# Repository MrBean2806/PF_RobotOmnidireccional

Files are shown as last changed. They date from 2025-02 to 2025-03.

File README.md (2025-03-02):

# PF_RobotOmnidireccional
## Proyecto Final de Grado - Ingeniería Electrónica
## _"Sistema de Control de Tracción de Bajo Nivel para un Robot Móvil"_

<div style="text-align: center;">
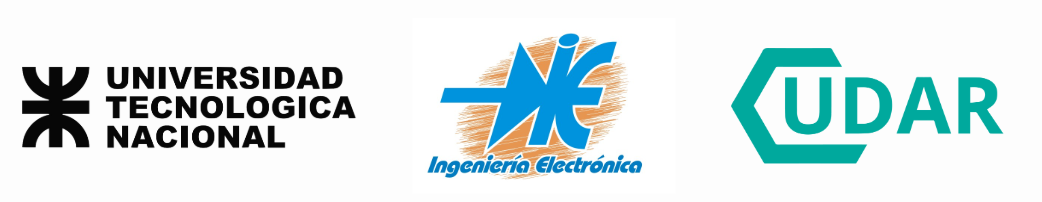
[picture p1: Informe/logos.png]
  
</div>

### Introducción
El proyecto se centra en el desarrollo de un sistema de control de tracción de bajo nivel para un robot móvil. Su principal objetivo es transformar los comandos de velocidad provenientes de la Computadora de Navegación en velocidades individuales para cada motor. Además, el sistema ejecuta un lazo de control de
velocidad en cada rueda, midiendo y ajustando la tensión media aplicada a cada motor. Finalmente, el sistema envía datos de velocidad estimada y aceleración a
la Computadora de Navegación. 

Este proyecto forma parte de una iniciativa más amplia del Centro Universitario
de Automatización y Robótica (CUDAR) de la UTN FRC, que abarca el diseño, desarrollo y construcción de un sistema de odometría multi-cámara montado en
un robot móvil, destinado a encontrar trayectorias eficientes en ambientes desconocidos y dinámicos.

### Contexto
A continuación se presenta el diagrama de contexto del sistema, que muestra
las entidades externas con las que éste interactúa y la naturaleza de dichas interacciones.

<div style="text-align: center;">
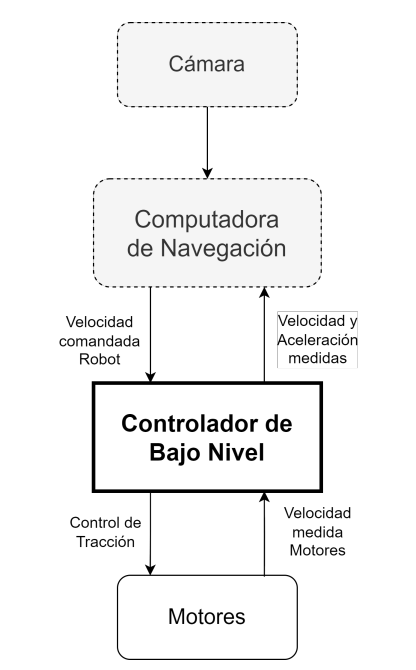
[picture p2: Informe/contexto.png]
  
</div>

Puede observarse que el sistema interactúa directamente con las siguientes entidades externas:
La Computadora de navegación (CDN), que provee la velocidad comandada y recibe la velocidad estimada y la aceleración medida por el Controlador de Bajo Nivel (CBN).
La gravedad y la aceleración, que son medidas para el uso de la Computadora de Navegación.
Los Motores del robot móvil, cuya velocidad es seteada y medida por el sistema.

### Arquitectura de Software

En la siguiente figura se muestra el diagrama conceptual de este proyecto, en el cual se pueden apreciar dos caminos principales.

<div style="text-align: center;">
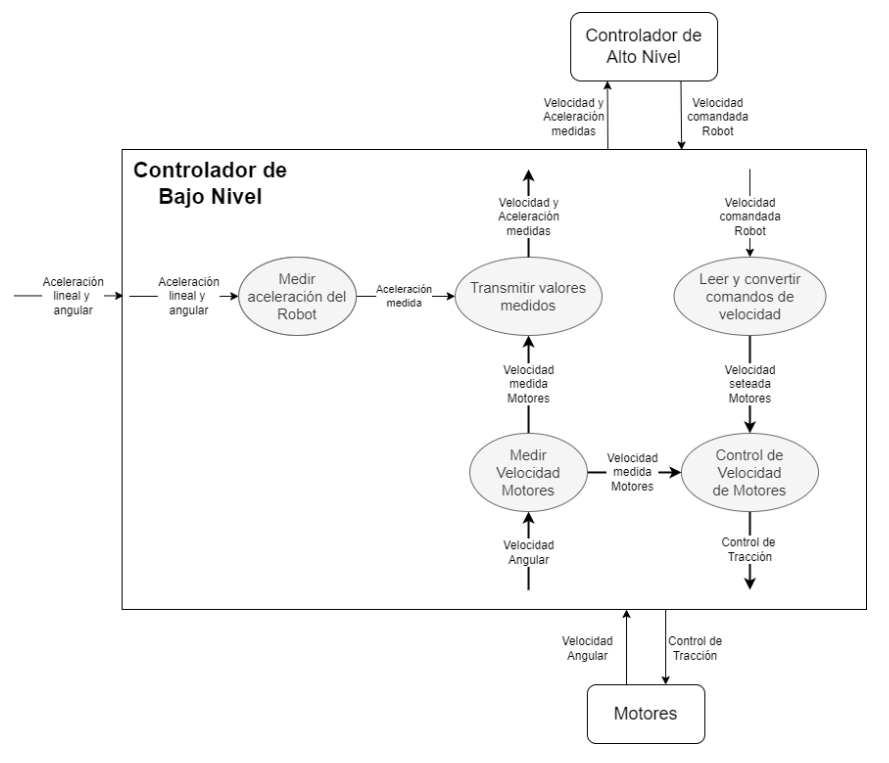
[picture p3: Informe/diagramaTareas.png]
  
</div>

En primer lugar, la velocidad comandada es enviada por la CDN y recibida por el CBN, la cual es convertida en comandos de velocidad para cada motor y finalmente se envía una señal para controlar los motores, teniendo en cuenta el valor de la velocidad medida de estos últimos. 

En segunda instancia, se miden tanto los valores de velocidad de cada motor, como los valores de aceleraciones del robot, los cuales son enviados finalmente al CDN.

_Para una explicación más detallada referirse al informe completo en la carpeta "Informe"_

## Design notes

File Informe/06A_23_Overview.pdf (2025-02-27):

### Universidad Tecnologica

´

### Nacional

### Facultad Regional Cordoba

´

# Proyecto Final

# Sistema de Control de Tracción de Bajo Nivel para un Robot Móvil

# Overview

### Profesores: Ing. Encina, Lucas Esteban Ing. Galleguillo, Juan Cayetano del Corazón Dr. Gaydou, David Alejandro

### Director de proyecto: Ing. Gutierrez, Guillermo

### Alumnos: Arias, Manuel Exequiel - 85187 Bean, Agustín - 78806

### 4 de julio de 2023

Proyecto Final | Overview

2

Proyecto Final | Overview

## 1. Overview

El proyecto descripto se basa en un sistema de control de tracción de bajo nivel para un robot móvil.
El propósito del mismo es convertir los comandos de velocidad enviados por un Controlador de Alto Nivel en velocidades individuales para cada motor. A su vez, se encarga de ejecutar un lazo de control de velocidad en cada rueda midiendo ésta y variando la tensión media aplicada a cada motor. Por último, envía datos recolectados de velocidad estimada y aceleración al Controlador de Alto Nivel.

El proyecto presentado está enmarcado dentro de uno más amplio, perteneciente al Centro Universitario de Automatización y Robótica (CUDAR) de la UTN FRC. El proyecto completo consiste en el diseño, desarrollo y construcción de un sistema de odometría multi-cámara, montado en un robot móvil, para encontrar trayectorias eficientes en ambientes desconocidos y dinámicos.

### 1.1. Contexto

A continuación se presenta el diagrama de contexto del sistema, que muestra las entidades externas con las que éste interactúa y la naturaleza de dichas interacciones.

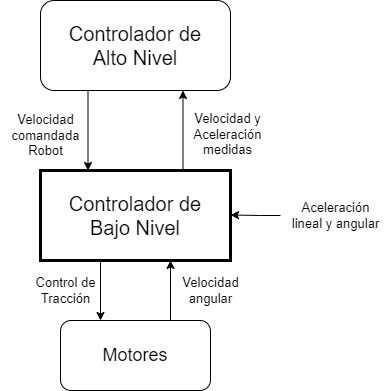
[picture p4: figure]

Figura 1: Diagrama de contexto

Puede observarse que el sistema interactúa directamente con las siguientes entidades externas:

El Controlador de Alto Nivel (CAN), que provee la velocidad comandada y recibe la velocidad estimada y la aceleración medida por el Controlador de Bajo Nivel (CBN).

3

Proyecto Final | Overview

La gravedad y la aceleración, que son medidas para el uso del Controlador de Alto Nivel.

Los Motores del robot móvil, cuya velocidad es seteada y medida por el sistema.

### Variables monitoreadas y controladas

Nombre | Tipo | Representación Física
Velocidad comandada Robot | Monitoreada Velocidad global deseada
| | recibida desde el CAN
Aceleración/Gravedad | Monitoreada Aceleración lineal y angular del
| | robot
Velocidad Angular Motores | Monitoreada Velocidad angular de cada
| | Motor
Velocidad y aceleración medidas Controlada | Velocidad y aceleración medidas
| | por el CBN que son enviadas al CAN
Tracción Motores | Controlada | Excitación aplicada a cada Motor

Cuadro 1: Variables monitoreadas y controladas preliminares

### 1.2. Metas

Las metas de alto nivel del sistema son:

G1 - Medir la velocidad y aceleración del robot y transmitir estos datos al Controlador de Alto Nivel.

G2 - Controlar la velocidad individual de los motores de forma que la velocidad global cumpla con la comandada por el Controlador de Alto Nivel.

## 2. Conceptos Operacionales

Caso de Uso 1: Inicialización de los Controladores
Este caso de uso describe cómo se configura el robot para que esté preparado para su operación normal.

Actor primario: Operario.

Precondición:
El robot está desenergizado.

4

Proyecto Final | Overview

Poscondición:
El robot está energizado.
Los controladores de alto y bajo nivel están inicializados y comunicados entre sí. El robot no se encuentra en movimiento.
El controlador de bajo nivel está desactivado.

Principal escenario exitoso:

1. El operador enciende el robot.
2. Ambos controladores se inicializan y activan sus módulos de comunicación.
3. El CBN inicializa sus módulos y periféricos.
4. Los controladores establecen una comunicación bidireccional entre sí.

Caso de Uso 2: Operación Normal del Controlador
Este caso de uso describe la operación normal del controlador de bajo nivel.

Actor primario: Controlador de Alto Nivel.

Precondición:
El robot está energizado.
El robot no se encuentra en movimiento
Los controladores de alto y bajo nivel están inicializados y comunicados entre sí El controlador de bajo nivel está desactivado

Poscondición: El robot no se encuentra en movimiento
El controlador de bajo nivel está desactivado

Principal escenario exitoso:

1. El CAN envía la señal de activación al de bajo nivel.
2. El CBN ingresa en su modo normal de operación.
3. El CBN recibe comandos de velocidad global y ajusta la velocidad de los Motores para cumplir con ella.
4. El CBN realiza mediciones de aceleración y velocidad y las transmite al CAN.
5. El CAN finaliza su operación y desactiva el CBN.

Caso de Uso 3: Mantener la velocidad seteada por el CAN
Este caso de uso describe cómo los comandos de velocidad global enviados por el

5

Proyecto Final | Overview

CAN son convertidos a señales de control adecuadas para los motores.

Actor primario: Controlador de Bajo Nivel.

Precondición:
Los controladores de alto y bajo nivel están inicializados y comunicados entre sí.

Poscondición:
Los controladores de alto y bajo nivel están inicializados y comunicados entre sí. La velocidad global del robot se condice con la comandada por el CAN.

Principal escenario exitoso:

1. El CBN recibe el comando de velocidad del CAN.
2. El CBN calcula las señales de control necesarias para cada Motor individual.
3. El CBN ejecuta un lazo de control comparando la señal calculada con la velocidad medida de cada Motor.
4. El CBN aplica la excitación correspondiente a cada Motor.
5. Se repiten los pasos del 1 al 4.

Caso de Uso 4: Realizar mediciones y enviarlas al CAN
Este caso de uso describe cómo el CBN realiza mediciones de velocidad de los Motores y de aceleración del robot y las envía al CAN.

Actor primario: Controlador de Bajo Nivel.

Precondición:
Los controladores de alto y bajo nivel están inicializados y comunicados entre sí.

Poscondición:
Los controladores de alto y bajo nivel están inicializados y comunicados entre sí. La velocidad global del robot se condice con la comandada por el CAN.

Principal escenario exitoso:

1. El CBN realiza la medición de aceleración angular y lineal.
2. El CBN realiza la medición de velocidad angular de cada motor.
3. El CBN envía los datos recolectados en los apartados anteriores al CAN.
4. Se repiten los pasos del 1 al 3.

6

Proyecto Final | | | | Overview

## 3. Entidades Externas

### Controlador de Alto Nivel

El Controlador de Alto Nivel envía comandos de velocidad al Controlador de Bajo Nivel, y recibe los datos de velocidad y aceleración transmitidos por éste.

Nombre | Tipo | Rango | Unidad | Interpretación Física
Velocidad comandada Robot | | | | Comando de Velocidad para el robot
Velocidad lineal (módulo) | Real [0...2.0] | m/s
Velocidad lineal (ángulo) | Real | [0...2π] | rad

Velocidad angular
(módulo) | Real [0...5.0] | rad/s

Cuadro 2: Variables Monitoreadas del Controlador de Bajo Nivel para el Controlador de Alto Nivel

Nombre | Tipo | Rango | Unidad | Interpretación Física
Velocidad Global estimada | | | | Velocidad calculada del robot con las mediciones efectuadas
Velocidad lineal (módulo) | Real [0...2.0] | m/s
Velocidad lineal (ángulo) | Real | [0...2π] | rad

Velocidad angular
(módulo) | Real [0...5.0] | rad/s

Cuadro 3: Variables Controladas del Controlador de Bajo Nivel para el Controlador de Alto Nivel

### Motores

Los motores de corriente continua son controlados por el CBN, y son los encargados de que el robot se desplace a la velocidad seteada por el CAN.

Nombre | Tipo | Rango | Unidad | Interpretación Física
Velocidad angular Real [-5.0...5.0] | rad/s | Velocidad angular del eje de cada Motor

Cuadro 5: Variables monitoreadas del Controlador de Bajo Nivel para los Motores

7

Proyecto Final | Overview
Nombre | Tipo | Rango | Unidad | Interpretación Física
Control de Tracción Real [0...1.00] | - | Ciclo de trabajo de la señal
| | | | PWM aplicada a cada motor

Cuadro 4: Variables controladas del Controlador de Bajo Nivel para los Motores

## 4. Requisitos Funcionales del Sistema

El Controlador de Bajo Nivel realiza 5 funciones de sistema: medir la aceleración del robot, medir la velocidad de los Motores, transmitir los valores medidos, leer y convertir comandos de velocidad, y el control de velocidad de los Motores.

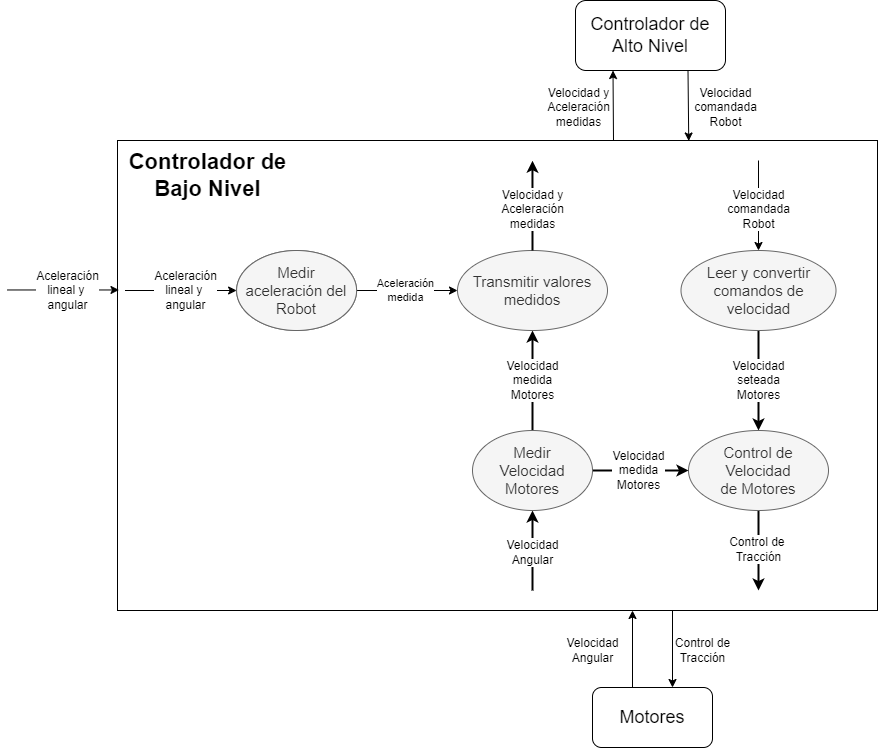
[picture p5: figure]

Figura 2: Funciones del sistema

Este sistema mide la aceleración del robot y la velocidad de cada Motor, para luego transmitirlas al Controlador de Alto Nivel. Este a su vez envía comandos ´

8

Proyecto Final | Overview

de velocidad, que son comparados con la velocidad medida de cada Motor para ajustar la tracción de los mismos de forma acorde.
Los requisitos de alto nivel para la función del Controlador de Bajo Nivel son:

REQ-CBN-1: El Controlador de Bajo Nivel deberá proveer el valor de la velocidad y la aceleración medida.
Motivo: Los valores de velocidad y aceleración del robot son críticos para que el Controlador de Alto Nivel pueda operar correctamente.

REQ-CBN-2: El Controlador de Bajo Nivel deberá setear el Control de Tracción.
Motivo: Para cumplir con la velocidad comandada por el Controlador de Alto Nivel es necesario ajustar la tracción de los Motores de forma acorde.
Nombre | Tipo Rango | Unidad Interpretación Física

Aceleración
medida | Real | [-10.0...10.0] m/s² | Aceleración medida del robot

Velocidad medida
Motores | Real | [-5.0...5.0] | rad/s | Velocidad angular medida en cada Motor

Velocidad seteada
Motores | Real | [-5.0...5.0] | rad/s | Velocidad angular seteada para cada Motor

Cuadro 6: Variables internas de la función del CBN

9

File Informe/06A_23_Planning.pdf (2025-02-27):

Id | Nombre de tarea | Duración | Comienzo | Fin
1 | Definición de requerimientos | 36 días | vie 12/5/23 | vie 30/6/23
2 | Diseño Conceptual | 26 días | vie 26/5/23 | vie 30/6/23
3 | Diseño de Arquitectura de Hardware | 10 días | lun 3/7/23 | vie 14/7/23
4 | Desarrollo de Hardware21 días | lun 17/7/23 | lun 14/8/23
5 | Diseño de Arquitectura de Software | 10 días | lun 17/7/23 | vie 28/7/23
6 | Desarrollo de Software | 21 días | lun 31/7/23 | lun 28/8/23
7 | Integración y puesta en marcha | 7 días | mar 29/8/23 | mié 6/9/23
8 | Validación y Ensayo | 2 días | jue 7/9/23 | vie 8/9/23
30 | 7 | 14 | 21 | 28 | 4 | 11 | 18 | 25 | 2 | 9 | 16 | 23 | 30 | 6 | 13 | 20 | 27 | 3 | 10
may '23 | jun '23 | jul '23 | ago '23 | sep '23

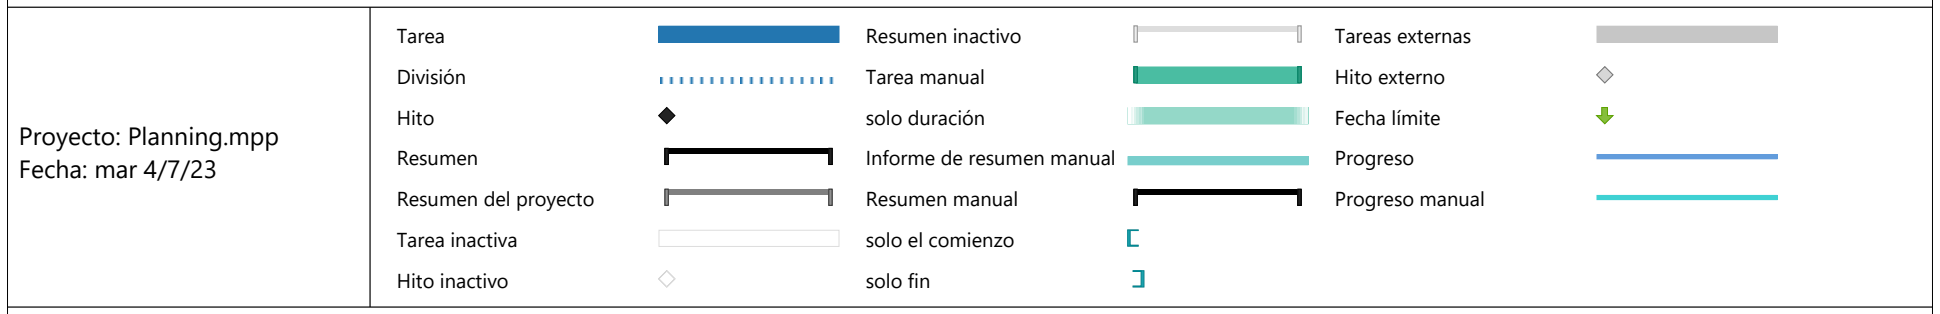
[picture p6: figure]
Tarea; División; Hito; Resumen; Resumen del proyecto; Tarea inactiva; Hito inactivo; Resumen inactivo; Tarea manual; solo duración; Informe de resumen manual; Resumen manual; solo el comienzo; solo fin; Tareas externas; Hito externo; Fecha límite; Progreso; Progreso manual; Proyecto: Planning.mpp Fecha: mar 4/7/23

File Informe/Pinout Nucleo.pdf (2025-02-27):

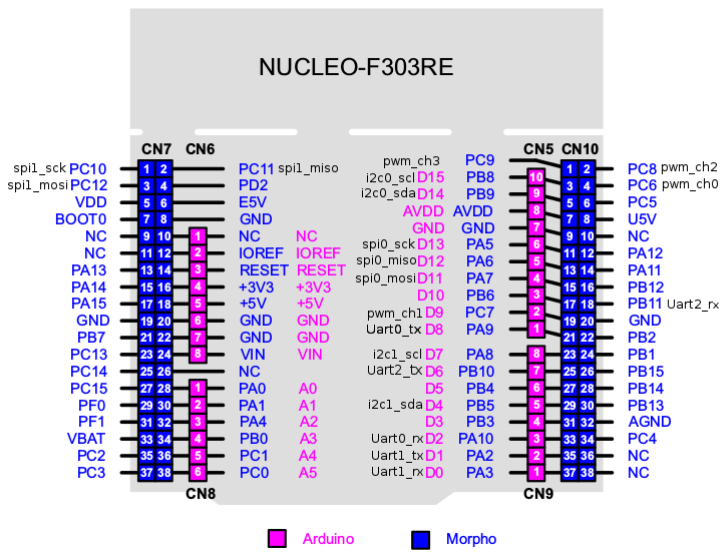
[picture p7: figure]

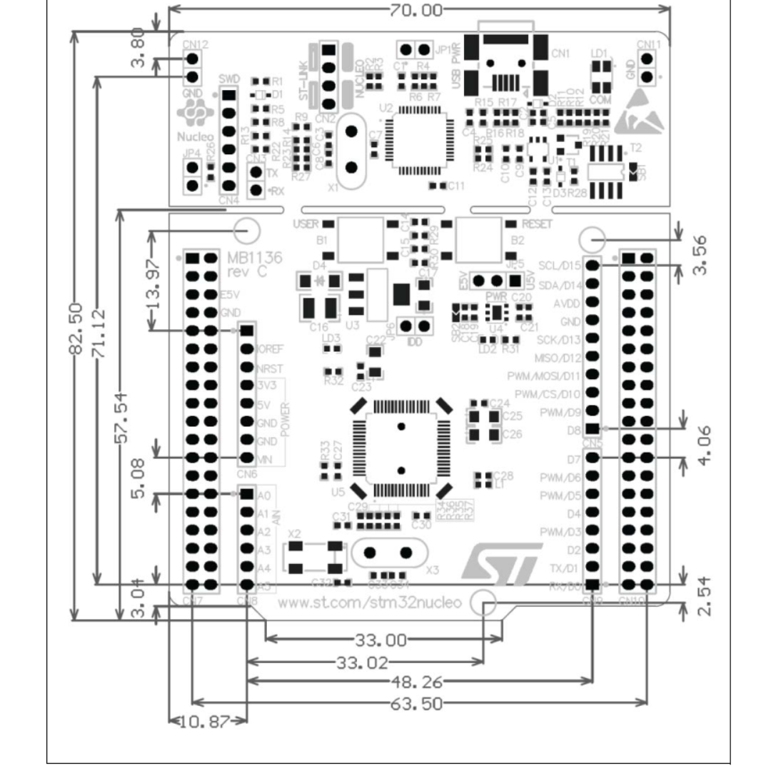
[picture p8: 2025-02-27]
Informe/Dimensiones Nucleo.png

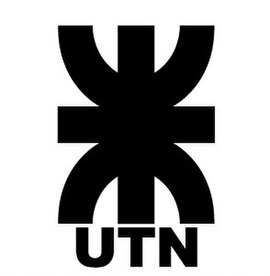
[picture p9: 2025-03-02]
Informe/utn.png

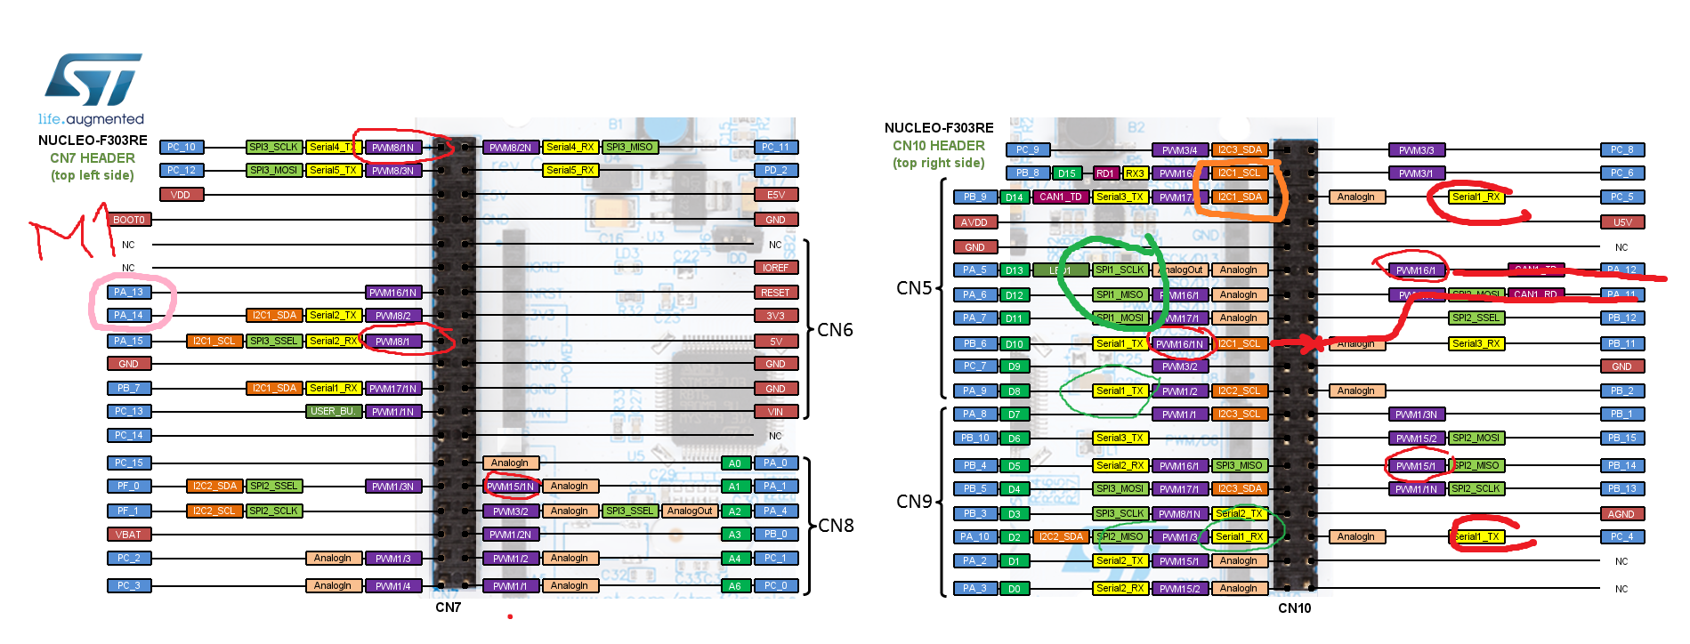
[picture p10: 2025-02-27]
Informe/Pinout Nucleo Completo.png

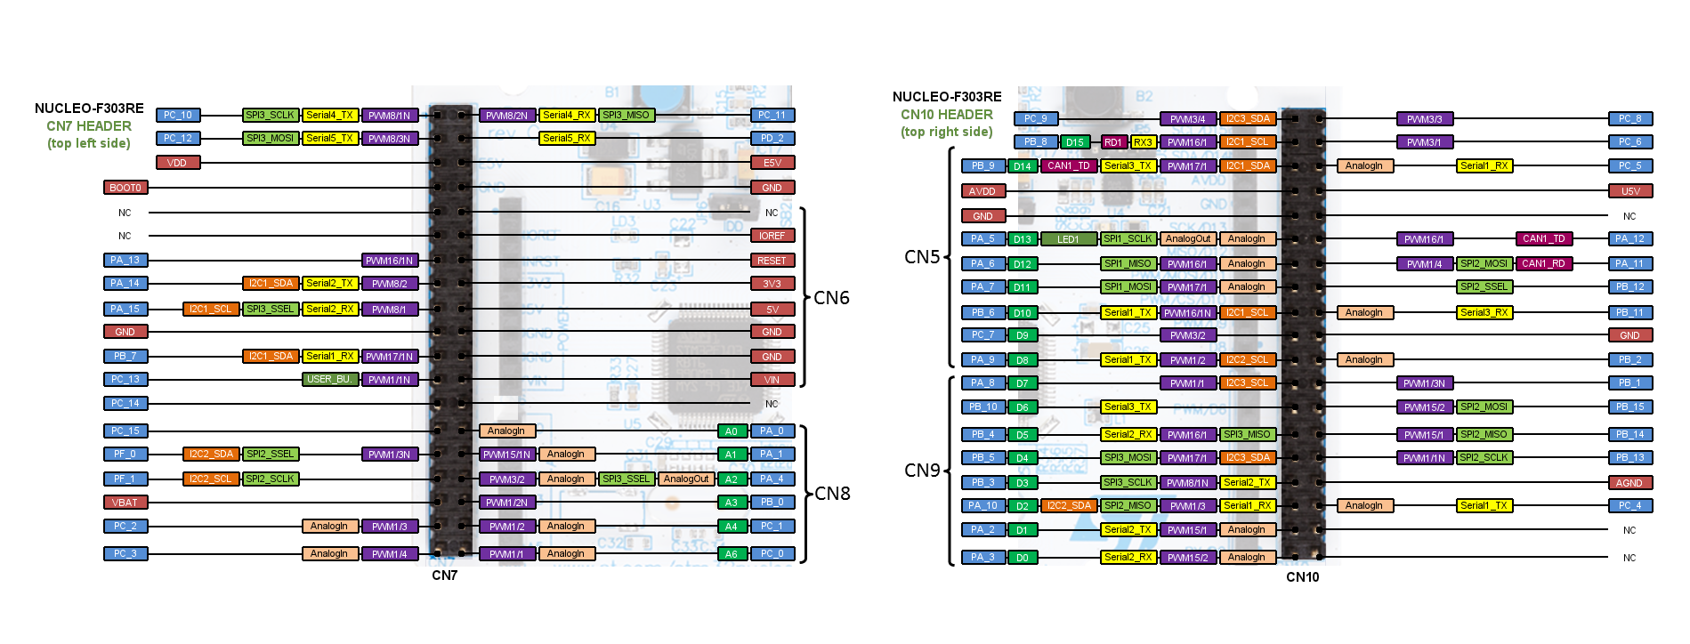
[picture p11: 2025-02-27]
Informe/Pinout Nucleo Completo v1.png

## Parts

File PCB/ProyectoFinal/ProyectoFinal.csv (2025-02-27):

Source: | C:\Users\agusb\OneDrive\Escritorio\Proyecto Final\PCB\ProyectoFinal\ProyectoFinal.kicad_sch
Date: | 26/11/2023 19:50:53
Tool: | Eeschema (6.0.10)
Generator: | C:\Program Files\KiCad\6.0\bin\scripting\plugins/bom_csv_grouped_by_value.py
Component Count: | 33
Individual Components:
Item | Qty | Reference(s) | Value | LibPart | Footprint | Datasheet
 |  | C1 | 100n | Device:C | Capacitor_THT:C_Disc_D4.3mm_W1.9mm_P5.00mm | ~
 |  | D1 | LED | Device:LED | LED_THT:LED_D5.0mm | ~
 |  | J1 | Conector_Alim_PuenteH1 | Connector:Conn_01x02_Female | Connector_JST:JST_EH_B2B-EH-A_1x02_P2.50mm_Vertical | ~
 |  | J2 | Conector_Encoder1 | Connector:Conn_01x04_Male | Connector_JST:JST_EH_B4B-EH-A_1x04_P2.50mm_Vertical | ~
 |  | J3 | Conector_Encoder3 | Connector:Conn_01x04_Male | Connector_JST:JST_EH_B4B-EH-A_1x04_P2.50mm_Vertical | ~
 |  | J4 | Conector_Alim_PuenteH2 | Connector:Conn_01x02_Female | Connector_JST:JST_EH_B2B-EH-A_1x02_P2.50mm_Vertical | ~
 |  | J5 | Conector_Encoder2 | Connector:Conn_01x04_Male | Connector_JST:JST_EH_B4B-EH-A_1x04_P2.50mm_Vertical | ~
 |  | J6 | Conector_Encoder4 | Connector:Conn_01x04_Male | Connector_JST:JST_EH_B4B-EH-A_1x04_P2.50mm_Vertical | ~
 |  | J7 | Conector_Motor1 | Connector:Conn_01x02_Female | Connector_PinHeader_2.54mm:PinHeader_1x02_P2.54mm_Vertical | ~
 |  | J8 | Conector_Motor2 | Connector:Conn_01x02_Female | Connector_PinHeader_2.54mm:PinHeader_1x02_P2.54mm_Vertical | ~
 |  | J9 | Conector_Motor3 | Connector:Conn_01x02_Female | Connector_PinHeader_2.54mm:PinHeader_1x02_P2.54mm_Vertical | ~
 |  | J10 | Conector_Motor4 | Connector:Conn_01x02_Female | Connector_PinHeader_2.54mm:PinHeader_1x02_P2.54mm_Vertical | ~
 |  | J12 | Conector_Baterias | Connector:Conn_01x02_Male | Connector_JST:JST_EH_B2B-EH-A_1x02_P2.50mm_Vertical | ~
 |  | J14 | Conector_IMU | Connector_Generic:Conn_02x08_Odd_Even | CustomLib:Conector_IMU | ~
 |  | J15 | Conector_ConversorUSB | Connector:Conn_01x06_Female | Connector_PinSocket_2.54mm:PinSocket_1x06_P2.54mm_Horizontal | ~
 |  | J16 | Conector_Programador | Connector:Conn_01x04_Male | Connector_PinSocket_2.54mm:PinSocket_1x04_P2.54mm_Vertical | ~
 |  | R1 | 10k | Device:R | Resistor_THT:R_Axial_DIN0207_L6.3mm_D2.5mm_P10.16mm_Horizontal | ~
 |  | R2 | 10k | Device:R | Resistor_THT:R_Axial_DIN0207_L6.3mm_D2.5mm_P10.16mm_Horizontal | ~
 |  | R3 | 220 | Device:R | Resistor_THT:R_Axial_DIN0207_L6.3mm_D2.5mm_P10.16mm_Horizontal | ~
 |  | R4 | 220 | Device:R | Resistor_THT:R_Axial_DIN0207_L6.3mm_D2.5mm_P10.16mm_Horizontal | ~
 |  | R5 | 10k | Device:R | Resistor_THT:R_Axial_DIN0207_L6.3mm_D2.5mm_P10.16mm_Horizontal | ~
 |  | R6 | 10k | Device:R | Resistor_THT:R_Axial_DIN0207_L6.3mm_D2.5mm_P10.16mm_Horizontal | ~
 |  | R7 | 220 | Device:R | Resistor_THT:R_Axial_DIN0207_L6.3mm_D2.5mm_P10.16mm_Horizontal | ~
 |  | R8 | 220 | Device:R | Resistor_THT:R_Axial_DIN0207_L6.3mm_D2.5mm_P10.16mm_Horizontal | ~
 |  | R9 | R | Device:R | Resistor_THT:R_Axial_DIN0207_L6.3mm_D2.5mm_P10.16mm_Horizontal | ~
 |  | R10 | R | Device:R | Resistor_THT:R_Axial_DIN0207_L6.3mm_D2.5mm_P10.16mm_Horizontal | ~
 |  | R11 | R | Device:R | Resistor_THT:R_Axial_DIN0207_L6.3mm_D2.5mm_P10.16mm_Horizontal | ~
 |  | R12 | 4K7 | Device:R | Resistor_THT:R_Axial_DIN0207_L6.3mm_D2.5mm_P10.16mm_Horizontal | ~
 |  | R13 | 4K7 | Device:R | Resistor_THT:R_Axial_DIN0207_L6.3mm_D2.5mm_P10.16mm_Horizontal | ~
 |  | SW1 | SW_SPST | Switch:SW_SPST | CustomLib:SW_SPST | ~
 |  | U1 | INA219_Module | CustomLib:INA219_Module | CustomLib:INA219_Module
 |  | U2 | LM2596_Module | CustomLib:LM2596_Module | CustomLib:DCDC_StepDown_LM2596
 |  | U3 | Nucleo_F303RE | CustomLib:Nucleo_F303RE | CustomLib:Nucleo_F303RE
Collated Components:
Item | Qty | Reference(s) | Value | LibPart | Footprint | Datasheet
1 | 1 | C1 | 100n | Device:C | Capacitor_THT:C_Disc_D4.3mm_W1.9mm_P5.00mm | ~
2 | 1 | D1 | LED | Device:LED | LED_THT:LED_D5.0mm | ~
3 | 1 | J1 | Conector_Alim_PuenteH1 | Connector:Conn_01x02_Female | Connector_JST:JST_EH_B2B-EH-A_1x02_P2.50mm_Vertical | ~
4 | 1 | J2 | Conector_Encoder1 | Connector:Conn_01x04_Male | Connector_JST:JST_EH_B4B-EH-A_1x04_P2.50mm_Vertical | ~
5 | 1 | J3 | Conector_Encoder3 | Connector:Conn_01x04_Male | Connector_JST:JST_EH_B4B-EH-A_1x04_P2.50mm_Vertical | ~
6 | 1 | J4 | Conector_Alim_PuenteH2 | Connector:Conn_01x02_Female | Connector_JST:JST_EH_B2B-EH-A_1x02_P2.50mm_Vertical | ~
7 | 1 | J5 | Conector_Encoder2 | Connector:Conn_01x04_Male | Connector_JST:JST_EH_B4B-EH-A_1x04_P2.50mm_Vertical | ~
8 | 1 | J6 | Conector_Encoder4 | Connector:Conn_01x04_Male | Connector_JST:JST_EH_B4B-EH-A_1x04_P2.50mm_Vertical | ~
9 | 1 | J7 | Conector_Motor1 | Connector:Conn_01x02_Female | Connector_PinHeader_2.54mm:PinHeader_1x02_P2.54mm_Vertical | ~
10 | 1 | J8 | Conector_Motor2 | Connector:Conn_01x02_Female | Connector_PinHeader_2.54mm:PinHeader_1x02_P2.54mm_Vertical | ~
11 | 1 | J9 | Conector_Motor3 | Connector:Conn_01x02_Female | Connector_PinHeader_2.54mm:PinHeader_1x02_P2.54mm_Vertical | ~
12 | 1 | J10 | Conector_Motor4 | Connector:Conn_01x02_Female | Connector_PinHeader_2.54mm:PinHeader_1x02_P2.54mm_Vertical | ~
13 | 1 | J12 | Conector_Baterias | Connector:Conn_01x02_Male | Connector_JST:JST_EH_B2B-EH-A_1x02_P2.50mm_Vertical | ~
14 | 1 | J14 | Conector_IMU | Connector_Generic:Conn_02x08_Odd_Even | CustomLib:Conector_IMU | ~
15 | 1 | J15 | Conector_ConversorUSB | Connector:Conn_01x06_Female | Connector_PinSocket_2.54mm:PinSocket_1x06_P2.54mm_Horizontal | ~
16 | 1 | J16 | Conector_Programador | Connector:Conn_01x04_Male | Connector_PinSocket_2.54mm:PinSocket_1x04_P2.54mm_Vertical | ~
17 | 4 | R1, R2, R5, R6 | 10k | Device:R | Resistor_THT:R_Axial_DIN0207_L6.3mm_D2.5mm_P10.16mm_Horizontal | ~
18 | 4 | R3, R4, R7, R8 | 220 | Device:R | Resistor_THT:R_Axial_DIN0207_L6.3mm_D2.5mm_P10.16mm_Horizontal | ~
19 | 3 | R9, R10, R11 | R | Device:R | Resistor_THT:R_Axial_DIN0207_L6.3mm_D2.5mm_P10.16mm_Horizontal | ~
20 | 2 | R12, R13 | 4K7 | Device:R | Resistor_THT:R_Axial_DIN0207_L6.3mm_D2.5mm_P10.16mm_Horizontal | ~
21 | 1 | SW1 | SW_SPST | Switch:SW_SPST | CustomLib:SW_SPST | ~
22 | 1 | U1 | INA219_Module | CustomLib:INA219_Module | CustomLib:INA219_Module
23 | 1 | U2 | LM2596_Module | CustomLib:LM2596_Module | CustomLib:DCDC_StepDown_LM2596
24 | 1 | U3 | Nucleo_F303RE | CustomLib:Nucleo_F303RE | CustomLib:Nucleo_F303RE

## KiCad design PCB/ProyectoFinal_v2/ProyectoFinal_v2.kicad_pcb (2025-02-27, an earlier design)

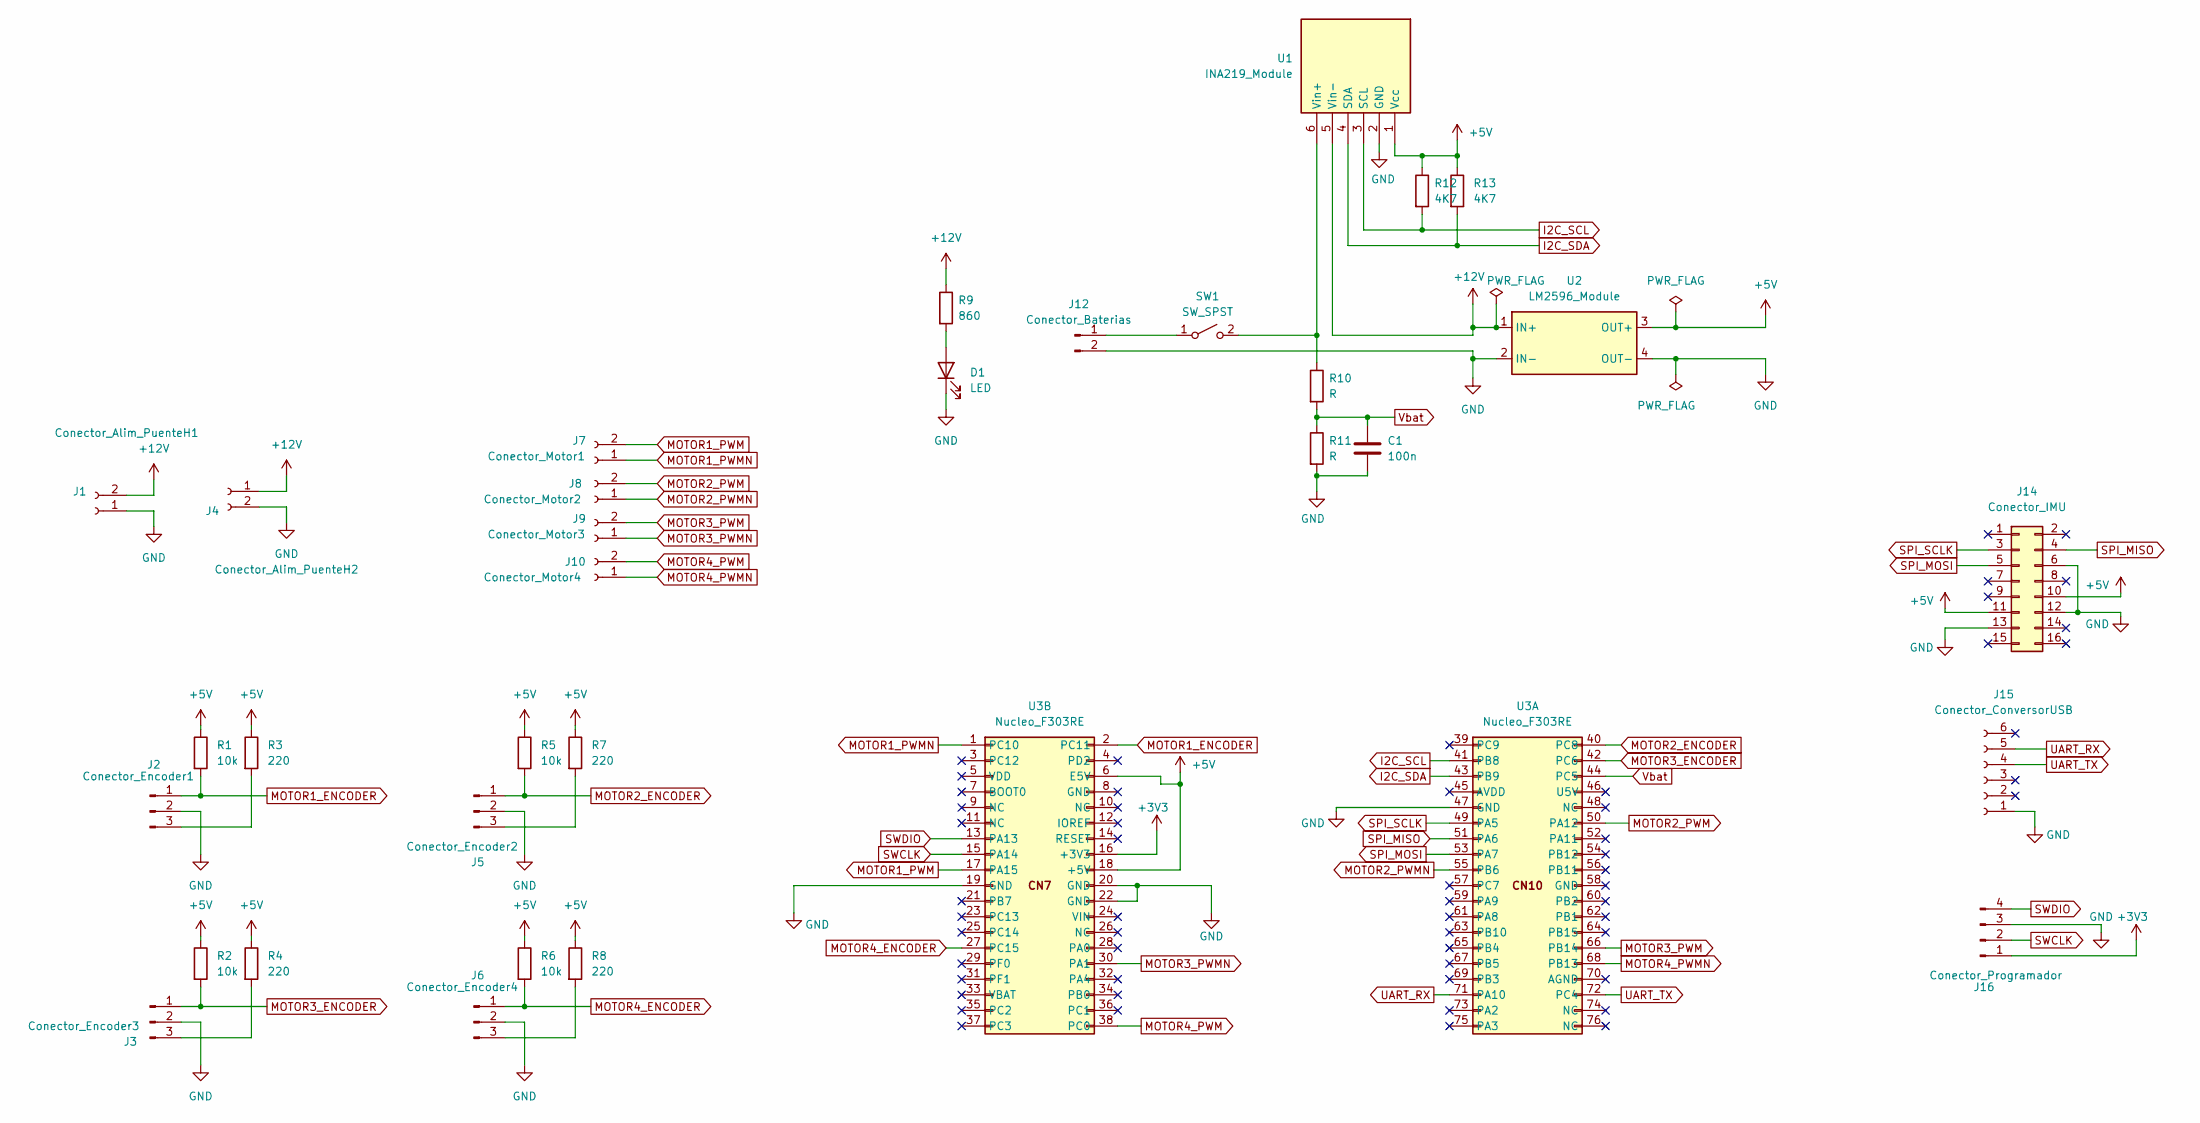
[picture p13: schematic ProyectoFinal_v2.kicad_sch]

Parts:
C1: 100n; C_Disc_D4.3mm_W1.9mm_P5.00mm
D1: LED; LED_D5.0mm
J1: Conector_Alim_PuenteH1; JST_EH_B2B-EH-A_1x02_P2.50mm_Vertical
J2: Conector_Encoder1; JST_EH_B3B-EH-A_1x03_P2.50mm_Vertical
J3: Conector_Encoder3; JST_EH_B3B-EH-A_1x03_P2.50mm_Vertical
J4: Conector_Alim_PuenteH2; JST_EH_B2B-EH-A_1x02_P2.50mm_Vertical
J5: Conector_Encoder2; JST_EH_B3B-EH-A_1x03_P2.50mm_Vertical
J6: Conector_Encoder4; JST_EH_B3B-EH-A_1x03_P2.50mm_Vertical
J7: Conector_Motor1; PinHeader_1x02_P2.54mm_Vertical
J8: Conector_Motor2; PinHeader_1x02_P2.54mm_Vertical
J9: Conector_Motor3; PinHeader_1x02_P2.54mm_Vertical
J10: Conector_Motor4; PinHeader_1x02_P2.54mm_Vertical
J12: Conector_Baterias; JST_EH_B2B-EH-A_1x02_P2.50mm_Vertical
J14: Conector_IMU
J15: Conector_ConversorUSB; PinSocket_1x06_P2.54mm_Horizontal
J16: Conector_Programador; PinSocket_1x04_P2.54mm_Vertical
R1, R2, R5, R6: 10k; R_Axial_DIN0207_L6.3mm_D2.5mm_P10.16mm_Horizontal
R3, R4, R7, R8: 220; R_Axial_DIN0207_L6.3mm_D2.5mm_P10.16mm_Horizontal
R9: 860; R_Axial_DIN0207_L6.3mm_D2.5mm_P10.16mm_Horizontal
R10, R11: R; R_Axial_DIN0207_L6.3mm_D2.5mm_P10.16mm_Horizontal
R12, R13: 4K7; R_Axial_DIN0207_L6.3mm_D2.5mm_P10.16mm_Horizontal
SW1: SW_SPST
U1: INA219_Module
U2: LM2596_Module; DCDC_StepDown_LM2596
U3: Nucleo_F303RE

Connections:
+3V3: J16.1, U3.16 (+3V3)
+5V: J14.10, J14.11, R1.1, R2.1, R3.1, R4.1, R5.1, R6.1, R7.1, R8.1, R12.1, R13.1, U1.1 (Vcc), U2.3 (OUT+), U3.6 (E5V), U3.18 (+5V)
+12V: J1.2, J4.1, R9.1, U1.5 (Vin-), U2.1 (IN+)
GND: C1.2, D1.1 (K), J1.1, J2.2, J3.2, J4.2, J5.2, J6.2, J12.2, J14.6, J14.12, J14.13, J15.1, J16.3, R11.2, U1.2 (GND), U2.2 (IN-), U2.4 (OUT-), U3.19 (GND), U3.20 (GND), U3.22 (GND), U3.47 (GND)
I2C_SCL: R12.2, U1.3 (SCL), U3.41 (PB8)
I2C_SDA: R13.2, U1.4 (SDA), U3.43 (PB9)
MOTOR1_ENCODER: J2.1, R1.2, U3.2 (PC11)
MOTOR1_PWM: J7.2, U3.17 (PA15)
MOTOR1_PWMN: J7.1, U3.1 (PC10)
MOTOR2_ENCODER: J5.1, R5.2, U3.40 (PC8)
MOTOR2_PWM: J8.2, U3.50 (PA12)
MOTOR2_PWMN: J8.1, U3.55 (PB6)
MOTOR3_ENCODER: J3.1, R2.2, U3.42 (PC6)
MOTOR3_PWM: J9.2, U3.66 (PB14)
MOTOR3_PWMN: J9.1, U3.30 (PA1)
MOTOR4_ENCODER: J6.1, R6.2, U3.27 (PC15)
MOTOR4_PWM: J10.2, U3.38 (PC0)
MOTOR4_PWMN: J10.1, U3.68 (PB13)
unnamed: D1.2 (A), R9.2
unnamed: J2.3, R3.2
unnamed: J3.3, R4.2
unnamed: J5.3, R7.2
unnamed: J6.3, R8.2
unnamed: J12.1, SW1.1 (A)
unnamed: R10.1, SW1.2 (B), U1.6 (Vin+)
SPI_MISO: J14.4, U3.51 (PA6)
SPI_MOSI: J14.5, U3.53 (PA7)
SPI_SCLK: J14.3, U3.49 (PA5)
SWCLK: J16.2, U3.15 (PA14)
SWDIO: J16.4, U3.13 (PA13)
UART_RX: J15.5, U3.71 (PA10)
UART_TX: J15.4, U3.72 (PC4)
Vbat: C1.1, R10.2, R11.1, U3.44 (PC5)

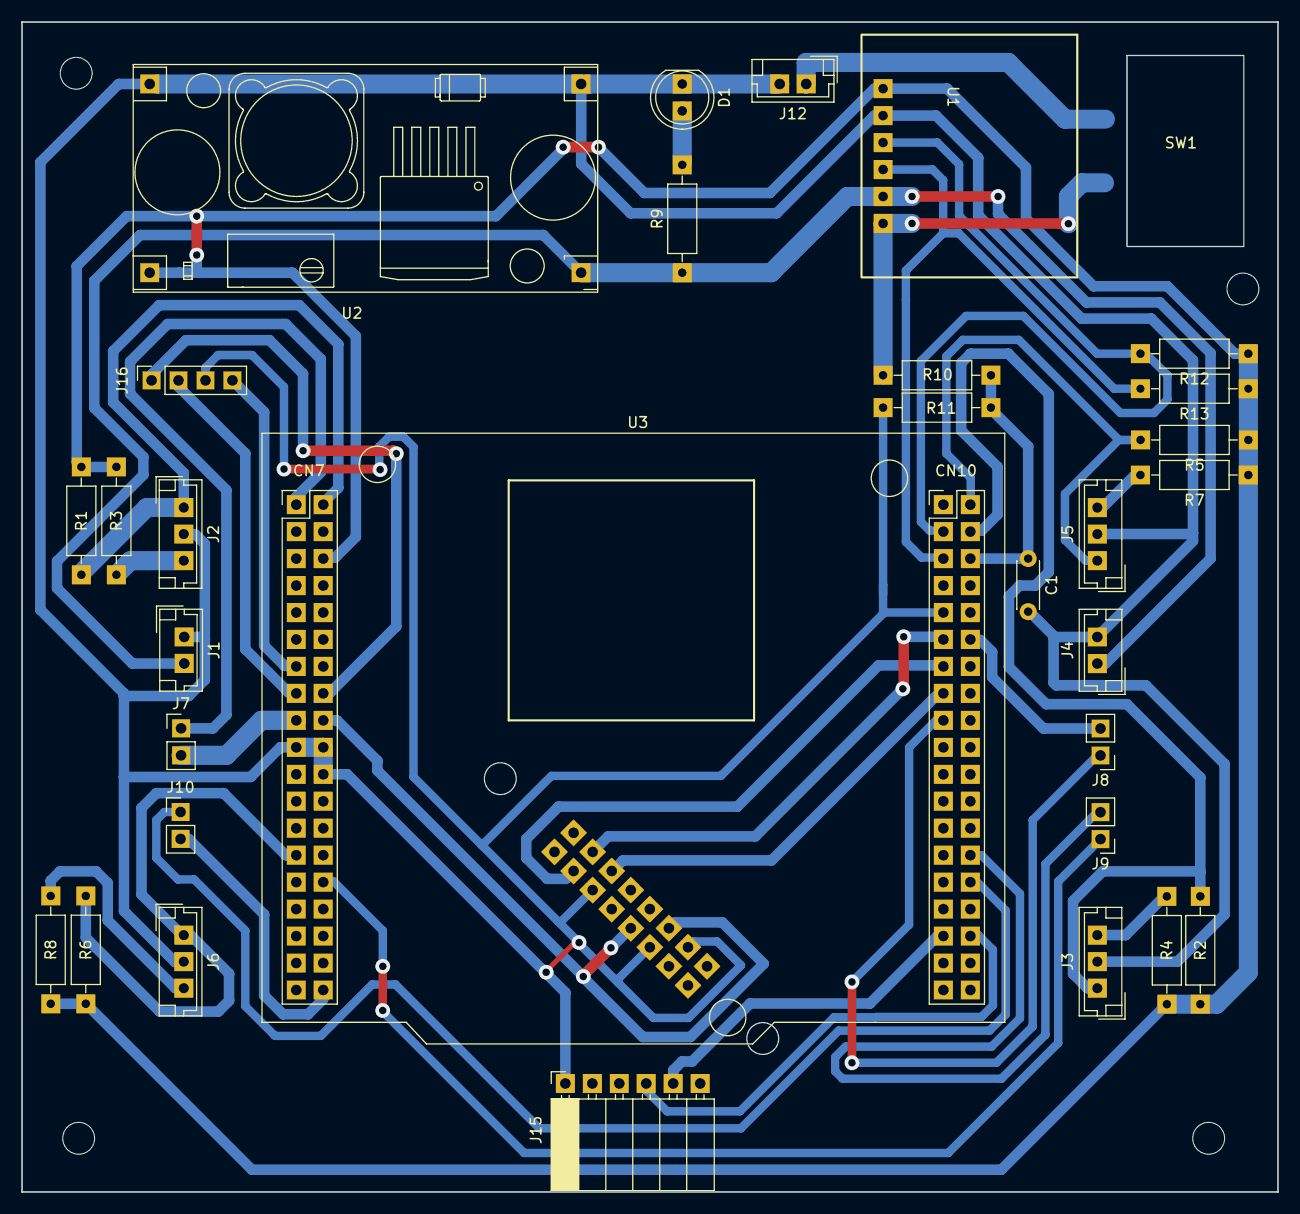
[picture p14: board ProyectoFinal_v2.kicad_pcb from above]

Board: 2 copper layers, 118.3 x 110.2 mm, 33 parts (1 on the bottom side), 33 nets.
